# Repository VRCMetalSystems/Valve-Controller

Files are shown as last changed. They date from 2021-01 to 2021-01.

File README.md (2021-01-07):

# Valve-Controller
Repo for the PCB files for the Valve controller

# Instructions for ordering

## Required Files
All the required files can be found in ./OrderFiles/
1. CAMFILES.zip
2. WhiteJewel-all-pos.csv
3. WhiteJewel.csv

# Steps
0. Download/clone this repo and extract it if needed.
1. Go to [JLCPCB.com](https://cart.jlcpcb.com/quote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)
2. Click on ***Add your gerber file***
3. Navigate to OrderFiles/CAMFILES.zip and upload it to the site. Wait till you see a preview of the board.
   - You can also drag and drop
4. Select the number of boards to be ordered in the ***PCB Qty*** text box.
    - You can order >50 boards but the assembly process has max of 50.
5. Make sure the ***Remove Order Number*** is set to ***YES***. 
6. Click on the ***SMT Assembly*** slider.
7. Click on ***Assemble Top side*** radio button to choose Top side assembly.
8. Accept the terms and conditions and click ***Confirm***
9. Upload the BOM and the CPL files in the appropriate spots
    - BOM file is called *WhiteJewel.csv*
    - CPL file is called *WhiteJewel-all-pos.csv*
10. Click Next 
11. If everything is processed successfully, The site will ask to confirm what parts to be placed. D5 and D6 are optional and can be removed by
clinking the trash can icon
12. After the cliking Next, the site will show you what it thnks the Assembled PCB will look like. 
    - Note that the site often gets the rotation of the parts wrong on the render. This is not indicative of the final board and is not an issue
13. Click on ***Save to cart*** to add the order to cart. 
14. Get a the credit card from the Purchasing department, Apply any "Coupons" that the site lets you and complete the order.
15. In addition, the following parts will have to be ordered via Digikey
      - 1x  377-1807-ND per board
      - 2x  609-3940-ND per board

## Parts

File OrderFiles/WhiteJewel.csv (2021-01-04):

Comment | Designator | Footprint | LCSC
LED | D1,D2,D3,D4 | Diode_SMD:D_0805_2012Metric_Pad1.15x1.40mm_HandSolder | C63855
‎BZX84C5V1LT3G | D5 | Diode_SMD:D_SOT-23_ANK
BZX84C5V1LT3G | D6 | Diode_SMD:D_SOT-23_ANK
Screw_Terminal_01x06 | J1,J2 | TerminalBlock:TerminalBlock_bornier-6_P5.08mm
BSS138 | Q1,Q2,Q3,Q4 | Package_TO_SOT_SMD:SOT-23 | C82045
5K | R1,R4,R5,R6,R7,R10 | Resistor_SMD:R_0805_2012Metric_Pad1.15x1.40mm_HandSolder | C78980
150 | R11,R12 | Resistor_SMD:R_0805_2012Metric_Pad1.15x1.40mm_HandSolder | C17471
5k | R2,R3,R8,R9,R13,R14,R15,R16,R17,R18 | Resistor_SMD:R_0805_2012Metric_Pad1.15x1.40mm_HandSolder | C78980
TestPoint | TP1,TP2,TP3,TP4,TP5,TP8 | TestPoint:TestPoint_Pad_D2.5mm
BTS4175SGA | U1,U2 | Package_SO:Infineon_PG-DSO-8-27_3.9x4.9mm_EP2.65x3mm | C152451

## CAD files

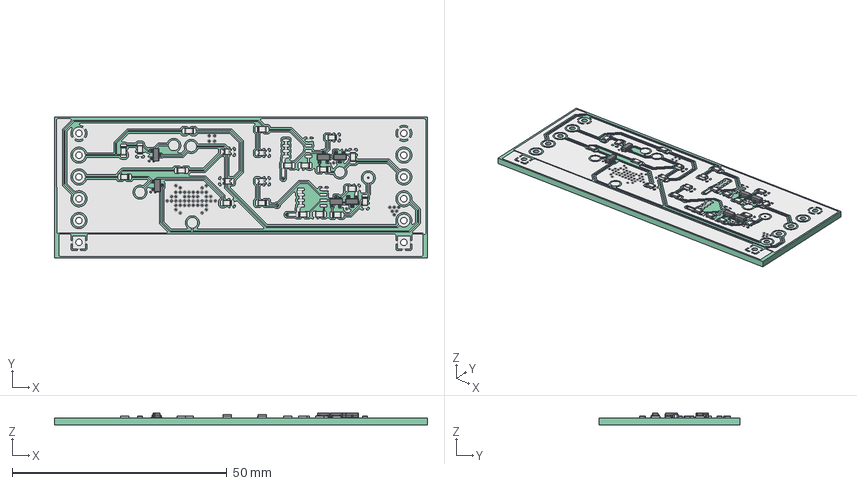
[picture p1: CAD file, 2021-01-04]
Board.FCStd
86.9 x 32.9 x 2.85 mm
Pcb_109f
topTracks_109f
botTracks_109f
R18_R_0805_2012Metric_5F767554
R17_R_0805_2012Metric_5F767543
D6_D_SOT_23_5F7671C8
R16_R_0805_2012Metric_5F7643F1
R15_R_0805_2012Metric_5F7643E0
R14_R_0805_2012Metric_5F7643CF
R13_R_0805_2012Metric_5F7643BE
R9_R_0805_2012Metric_5F76337B
R2_R_0805_2012Metric_5F763BB2
Q4_SOT_23_5F768331
Q3_SOT_23_5F763284
D5_D_SOT_23_5F7631A5
R12_R_0805_2012Metric_5F749649
R11_R_0805_2012Metric_5F749638
Q2_SOT_23_5F495DAD
Q1_SOT_23_5F495D98
R6_R_0805_2012Metric_5F43F12B
R4_R_0805_2012Metric_5F2C2516
R7_R_0805_2012Metric_5F2C51F8
R3_R_0805_2012Metric_5F2C2505
D1_D_0805_5F6D0465
D2_D_0805_5F2B2991
D3_D_0805_5F6CE9D5
D4_D_0805_5F2B29B7
R1_R_0805_2012Metric_5F2C3FB7
R5_R_0805_2012Metric_5F2B2A9A
R8_R_0805_2012Metric_5F6D041E
R10_R_0805_2012Metric_5F2B4EE9

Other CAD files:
Board.iges

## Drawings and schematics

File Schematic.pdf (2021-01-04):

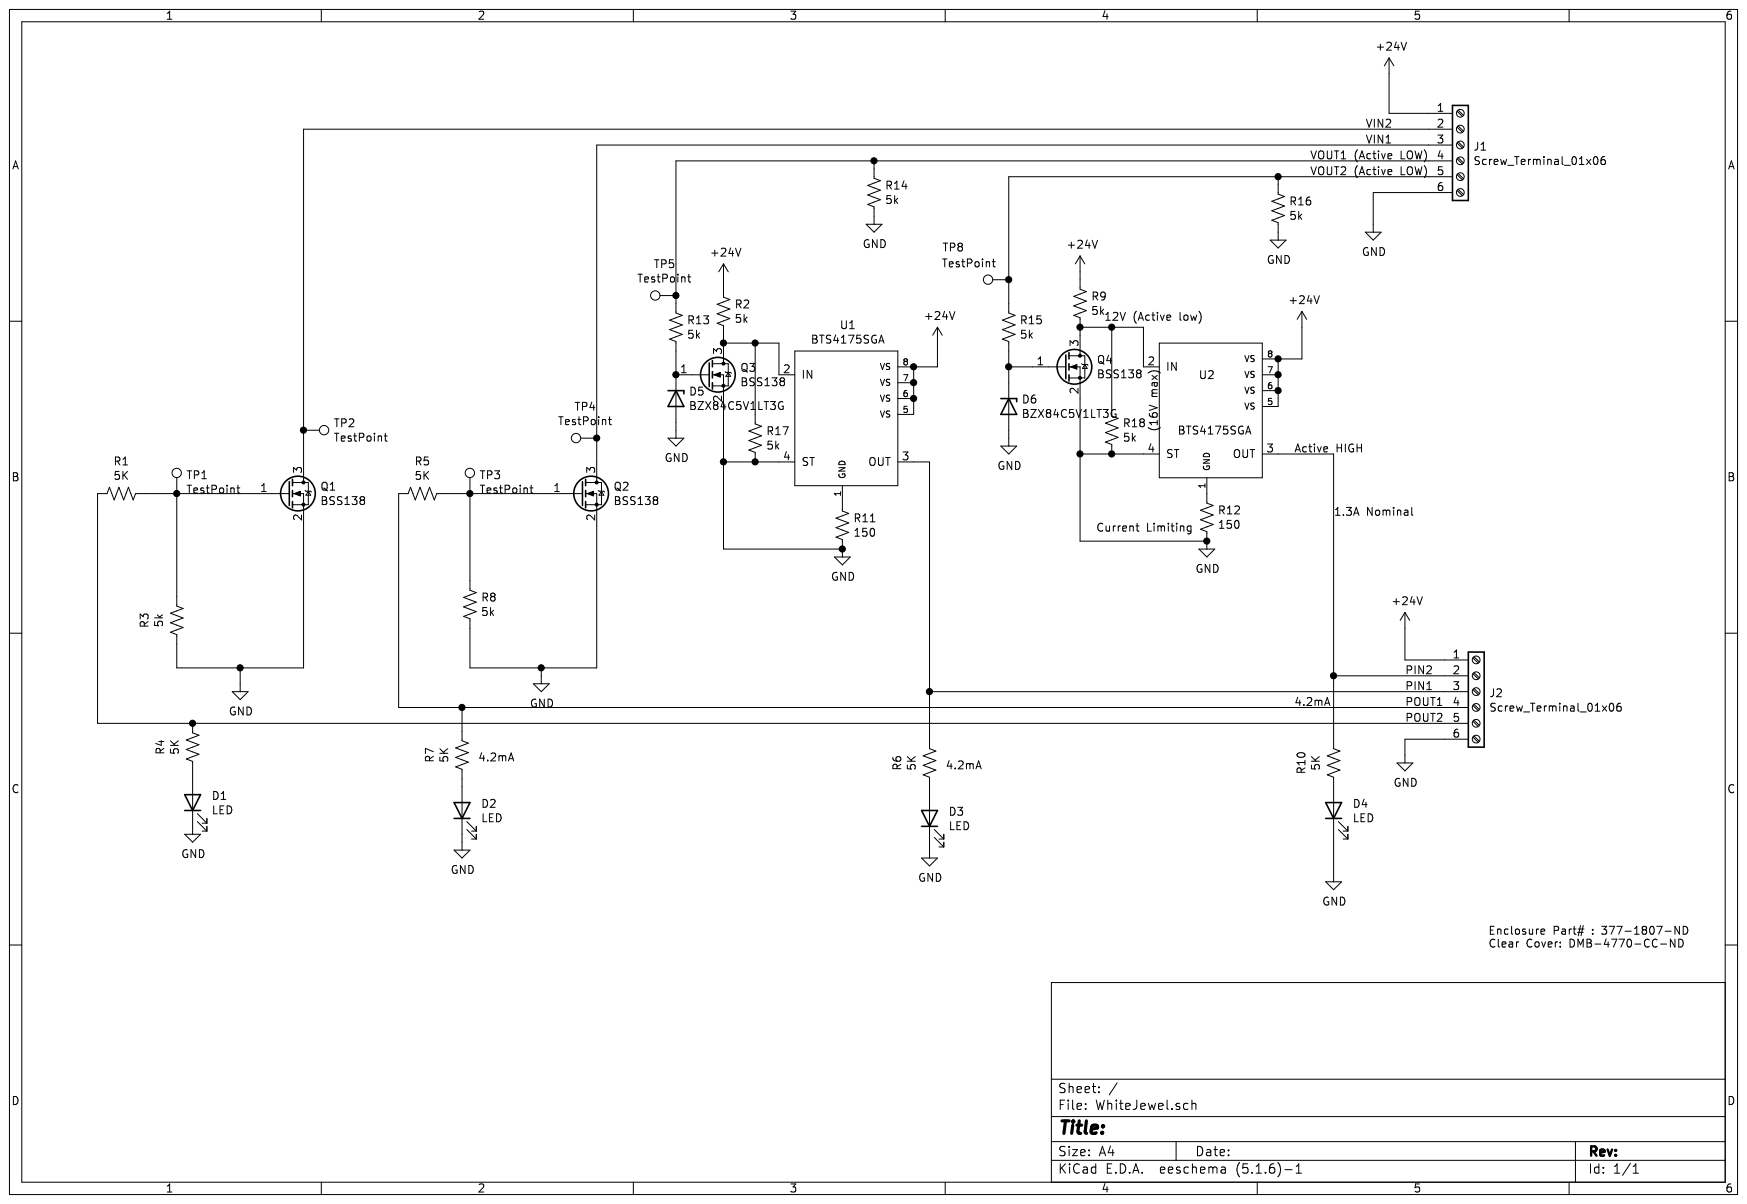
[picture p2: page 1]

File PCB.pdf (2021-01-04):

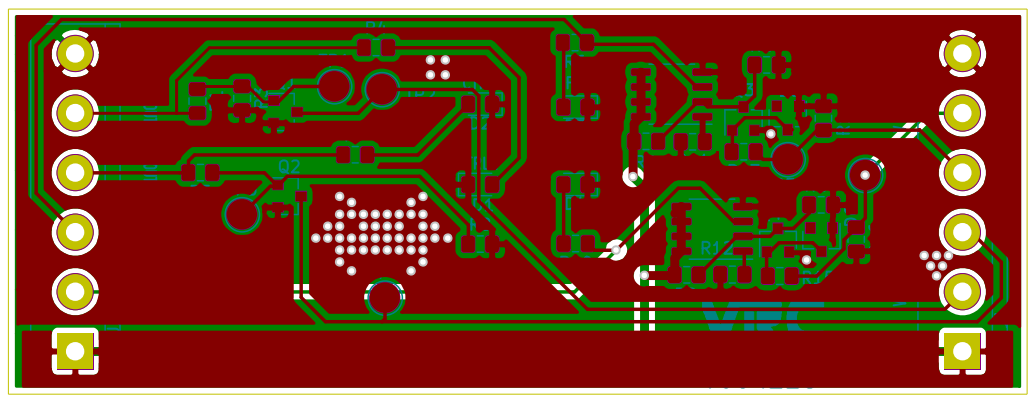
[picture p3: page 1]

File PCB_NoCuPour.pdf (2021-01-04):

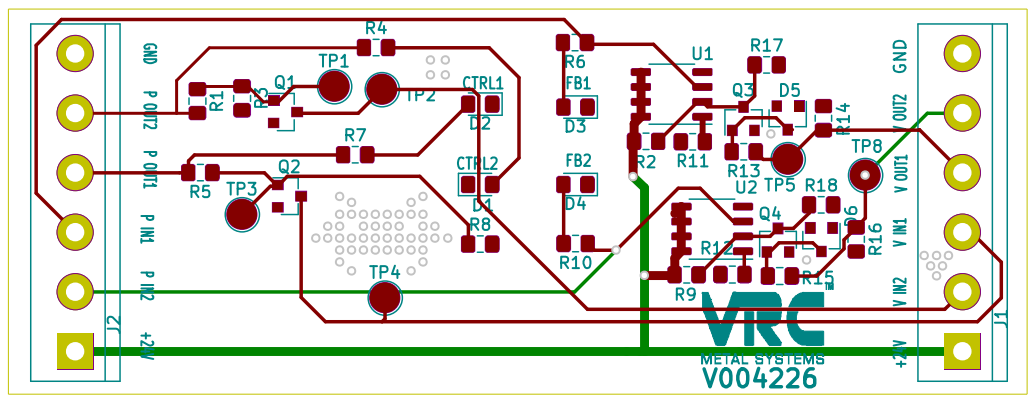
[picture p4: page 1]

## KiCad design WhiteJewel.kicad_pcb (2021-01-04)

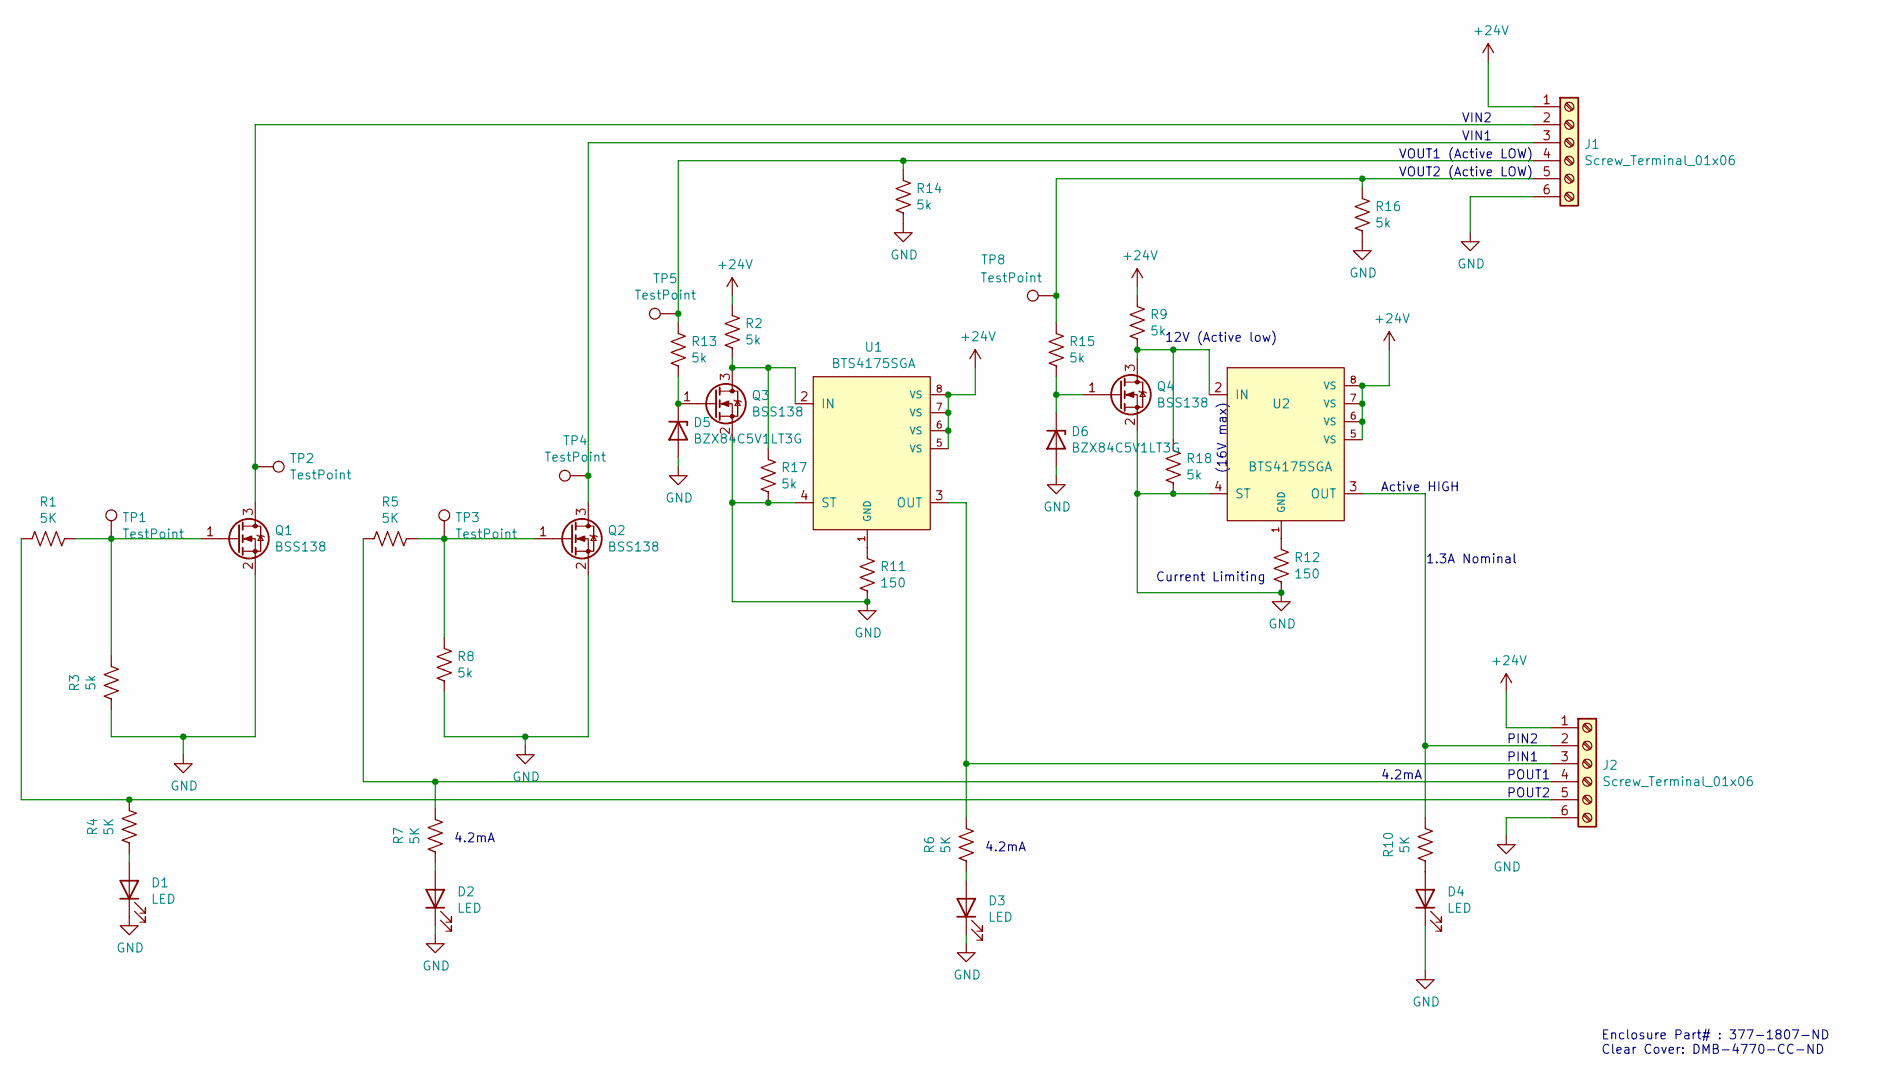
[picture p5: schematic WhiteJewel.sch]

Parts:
D1, D2, D3, D4: LED; D_0805_2012Metric_Pad1.15x1.40mm_HandSolder; LCSC C63855
D5: ‎BZX84C5V1LT3G; D_SOT-23_ANK
D6: BZX84C5V1LT3G; D_SOT-23_ANK
J1, J2: Screw_Terminal_01x06; TerminalBlock_bornier-6_P5.08mm; Digikey 609-3940-ND
Q1, Q2, Q3, Q4: BSS138; SOT-23; LCSC C82045
R1, R4, R5, R6, R7, R10: 5K; R_0805_2012Metric_Pad1.15x1.40mm_HandSolder; LCSC C78980
R2, R3, R8, R9, R13, R14, R15, R16, R17, R18: 5k; R_0805_2012Metric_Pad1.15x1.40mm_HandSolder; LCSC C78980
R11, R12: 150; R_0805_2012Metric_Pad1.15x1.40mm_HandSolder; LCSC C17471
TP1, TP2, TP3, TP4, TP5, TP8: TestPoint; TestPoint_Pad_D2.5mm
U1, U2: BTS4175SGA; Infineon_PG-DSO-8-27_3.9x4.9mm_EP2.65x3mm; LCSC C152451

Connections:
+24V: J1.1, J2.1, R2.1, R9.1, U1.5 (VS), U1.6 (VS), U1.7 (VS), U1.8 (VS), U2.5 (VS), U2.6 (VS), U2.7 (VS), U2.8 (VS)
GND: D1.1 (K), D2.1 (K), D3.1 (K), D4.1 (K), D5.2 (A), D6.2 (A), J1.6, J2.6, Q1.2 (S), Q2.2 (S), Q3.2 (S), Q4.2 (S), R3.2, R8.2, R11.2, R12.2, R14.2, R16.2, R17.2, R18.2, U1.4 (ST), U2.4 (ST)
unnamed: D1.2 (A), R4.2
unnamed: D2.2 (A), R7.2
unnamed: D3.2 (A), R6.2
unnamed: D4.2 (A), R10.2
unnamed: D5.1 (K), Q3.1 (G), R13.2
unnamed: D6.1 (K), Q4.1 (G), R15.2
unnamed: J1.2, Q1.3 (D), TP2.1
unnamed: J1.3, Q2.3 (D), TP4.1
unnamed: J1.4, R13.1, R14.1, TP5.1
unnamed: J1.5, R15.1, R16.1, TP8.1
unnamed: J2.2, R10.1, U2.3 (OUT)
unnamed: J2.3, R6.1, U1.3 (OUT)
unnamed: J2.4, R5.2, R7.1
unnamed: J2.5, R1.2, R4.1
unnamed: Q1.1 (G), R1.1, R3.1, TP1.1
unnamed: Q2.1 (G), R5.1, R8.1, TP3.1
unnamed: Q3.3 (D), R2.2, R17.1, U1.2 (IN)
unnamed: Q4.3 (D), R9.2, R18.1, U2.2 (IN)
unnamed: R11.1, U1.1 (GND)
unnamed: R12.1, U2.1 (GND)

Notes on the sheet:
4.2mA
1.3A Nominal
VIN2
VIN1
VOUT1 (Active LOW)
VOUT2 (Active LOW)
PIN2
PIN1
POUT1
POUT2
Current Limiting
12V (Active low)
(16V max)
Active HIGH
Enclosure Part# : 377-1807-ND‎ Clear Cover: DMB-4770-CC-ND

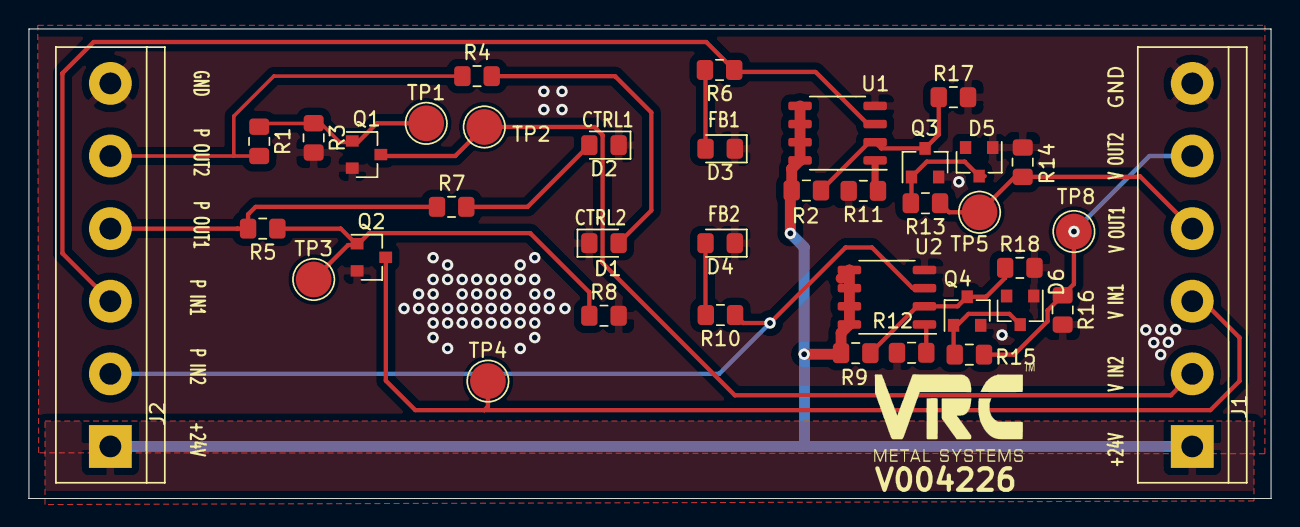
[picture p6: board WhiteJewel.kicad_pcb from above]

Board: 2 copper layers, 86.9 x 32.9 mm, 39 parts (0 on the bottom side), 22 nets.

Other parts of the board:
LG1: Logo; VRCLogo

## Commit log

2021-01-04 Ported files over from personal repo
    [Board.FCStd, Board.iges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]
2021-01-04 Added seperate folder for ordering
    [WhiteJewel.csv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]
2021-01-05 Added Enclosure and Terminal block part numbers
